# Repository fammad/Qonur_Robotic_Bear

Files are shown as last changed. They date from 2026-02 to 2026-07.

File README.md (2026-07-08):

# Qonur: Conversational AI in an Animatronic Bear




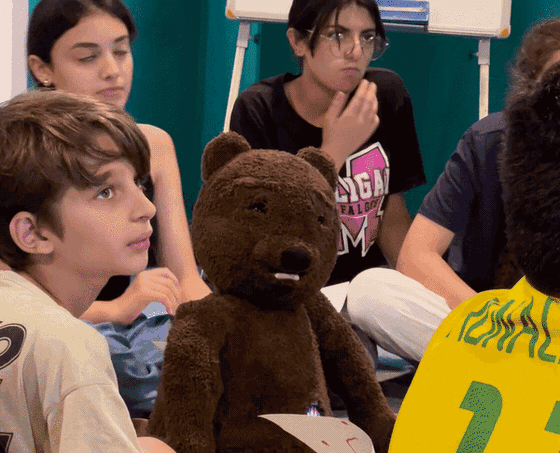
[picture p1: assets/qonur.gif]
Qonur live demo


Qonur is an AI-driven animatronic teddy bear that listens and speaks back in any language, including Azerbaijani. Behind the fur, a cloud language model, a speech pipeline, custom ESP32 firmware, and a 3D-printed actuated body run as one machine, while its mouth, eyes, and arms move in sync with the speech. It is built as a social robot for children, a familiar figure they can safely talk to about hard topics like bullying, or simply have as a friend. It performs in front of children and holds open conversations with them.

The architecture is a hybrid we call a robotic marionette. Gemini handles the conversation (speech in, generated reply, TTS out at 24 kHz) while an operator triggers arm and head gestures from a phone through Blynk. One ESP32 drives ten servos over a PCA9685 plus an 8-LED ring. A Python controller on a Raspberry Pi or laptop records the mic, calls Gemini, plays the reply, and streams mouth positions to the firmware as JSON over USB serial. The body is 3D printable from the pack in `hardware/`, about 40 cm and 2 kg in PLA.

**Watch it perform:** [live performance video](https://www.youtube.com/watch?v=doGUTJyK8F4). Same build, real audience.

## Why a marionette and not full autonomy

A cloud round trip takes several seconds and children do not wait. Scripted scenes need timing a language model will not give you. So the conversation is AI and the choreography stays human, one operator with a phone. We traded away the fully autonomous robot. In exchange, a show never stalls because the API did.

## What we tested

- The full loop on the assembled bear during live performances. Ask a question, the bear replies with moving mouth, blinking eyes, and listening LEDs.
- Two field deployments, one in a children's shelter and one in a rural village in the Lankaran region. Conversations were short-term, and the bear sometimes stayed with the children beyond the performance itself.
- The print pack on an Elegoo Neptune 4 Pro, 0.4 mm nozzle, PLA. 0.2 mm layers, 3 walls, 10 to 20 percent infill, supports only where needed.
- Not yet re-tested after this repo's code fixes: offline boot without WiFi, corrected mouth-sync duration, multi-turn conversation memory, and the inline audio path [PENDING TEST].

## Repository structure

```
main.py                    Python controller (recording, Gemini, TTS, serial)
firmware/qonur_firmware/   ESP32 sketch: servos, LEDs, serial protocol, Blynk
hardware/                  Print pack, Fusion 360 source, wiring, SETUP.md build guide
docs/                      Info pack and physical design PDFs
assets/                    Renders and demo media
```

## Build your own

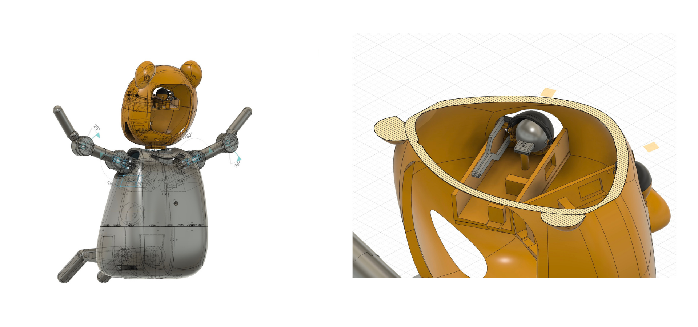
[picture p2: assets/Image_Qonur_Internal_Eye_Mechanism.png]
Internal eye mechanism


Body first. [`hardware/SETUP.md`](hardware/SETUP.md) covers printing (tested slicer settings included), what each body opening is for, assembly, and wiring. Print the pre-arranged 3MF or edit the Fusion 360 source and export your own.

Firmware. Open `firmware/qonur_firmware/qonur_firmware.ino` in Arduino IDE, install Adafruit PWM Servo Driver, Adafruit NeoPixel, ArduinoJson, and Blynk, fill in the WiFi and Blynk placeholders (optional), flash.

Controller, on Linux or Raspberry Pi:

```bash
sudo apt-get install -y portaudio19-dev libsndfile1 libasound2-dev
pip install -r requirements.txt
export GEMINI_API_KEY=your_key
python main.py
```

The bear's personality is one text block. Write your own `actor_prompt` in `main.py` and you have your own character, in whatever language and temperament you want. Set `ESP32_PORT` if your board is not on `/dev/ttyUSB0`.

The shipped defaults block content at the strictest Gemini safety thresholds, and in performances the scenario prompt further constrains what the bear says. Conversation memory is session-only and never written to disk.

## Limitations and failure analysis

- Mouth sync is open loop. Animation length comes from the PCM byte count and the pattern is a fixed 10-step sequence, so lips drift from phonemes on long replies.
- Every turn needs internet and Gemini quota. Latency stays at several seconds even with inline audio, long for a young audience.
- Push-to-talk is the Enter key in a terminal. No wake word, no voice activity detection.
- The firmware blinks autonomously every 3 seconds, holding a blocking 100 ms delay and overriding any eye command the controller sent mid-motion.
- Servos run open loop from an assumed 90 degree neutral. Skip mechanical calibration at assembly and every pose is off.
- Conversation memory re-sends recorded audio turns each request and is capped at 10 turn pairs, and the TTS cache rarely hits because replies at temperature 0.8 almost never repeat exactly.

## Future work

Long-term deployment comes first. Both field visits so far were short; the next step is leaving Qonur with a group of children for an extended period and assessing how their willingness to talk and their behaviour change over time. That requires personalization, a bear that remembers each child, which collides directly with children's data privacy. Designing that memory so no child gets profiled in the cloud is the problem we care about most.

On the technical list: a camera and a computer vision model so the bear reacts to who is in front of it, not only to voices, plus lower response latency and more expressive movement, both items that the live shows exposed.

## Status

Qonur was built and performed in 2025, in collaboration with Ritual Theater and Creativity Lab, funded by the Swiss Agency for Development and Cooperation (SDC). This repository merges the original code and mechanical design repositories, with their full history.

## Team

Fuad Mammadov and Jameel Hamzayev built and debugged the hardware and software together. Fuad led the robotics side (mechanics, 3D modeling, portable design), Jamil the AI side. Gülarə Aliyeva did 3D design and assembly, Nadejda Potaenko and Almaz Hasanzada the costume and appearance, Aynur Zarrintaj the script and dramaturgy.

## Credits & contact

Apache-2.0, see LICENSE. Credit appreciated.
Fuad Mammadov, [fammad.com](https://fammad.com) | Jameel Hamzayev, [github.com/jameelhamzayev](https://github.com/jameelhamzayev)

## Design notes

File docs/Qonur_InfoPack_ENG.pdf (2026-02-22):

Stage Performance and Role

Qonur is an inclusive actor robot bear powered by artificial intelligence. Designed for children and adolescents, Qonur takes part in story-based performances that address topics such as bullying, empathy, and awareness using the language of theater and interactive storytelling.
The teddy bear is a universal symbol of emotional comfort and safety for children. In many cultures, teddy bears are often considered a child's first friend – a symbolic figure to share fears with and feel secure around. Believing in the emotional power of this symbol, Qonur has been visually designed in the form of a teddy bear to build instant connection and trust with young audiences.
Qonur operates on a hybrid system, functioning both through AI-based automation and manual control via a mobile application, following the principles of a robotic marionette. It is portable and easy to transport. This system allows Qonur to respond dynamically to performance contexts and enables natural communication in Azerbaijani, English, and over 120 additional languages.

Based on its pre-programmed characteristics, Qonur performs as an actor in inclusive theatrical plays. It can take on the role of a narrator, a listener, or an interactive character that asks and answers questions.
While Qonur follows a prepared script, it is also able to respond adaptively and naturally to unexpected situations on stage. Although the performances initially focus on themes like inclusion and diversity, Qonur is easily adaptable to other social and educational topics in the future.

Who is Qonur and Why a Teddy Bear?

# QONUR ⁻ AI⁻Powered Robot Bear

Inclusion, Education, and Awareness Values

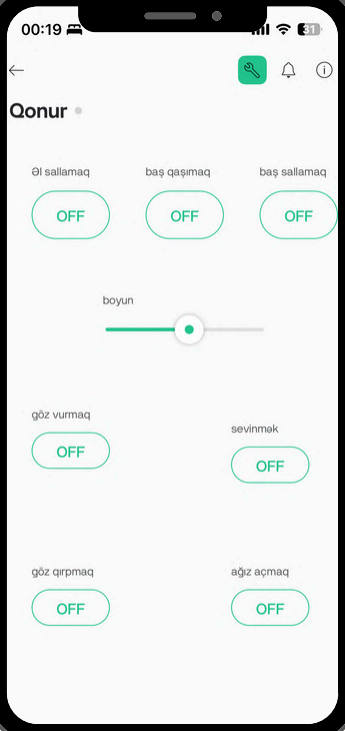
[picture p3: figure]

Technical Description (Hardware & Design) and AI Software System

Qonur is designed with an inclusive approach to openly communicate with children and adolescents who have physical and intellectual differences. Its communication style is simple, clear, and slow-paced, allowing children with diverse abilities to easily understand and respond. Through visual gestures, simplified language, eye contact, and body language, Qonur becomes accessible and understandable to all children. This helps it gain acceptance quickly, build trust, and effectively deliver inclusive educational and social messages.
Qonur serves as a practical and motivational tool in both educational and social awareness contexts. It can be used in various formats within schools, festivals, seminars, and educational laboratories—such as anti-bullying programs, empathy and social skills workshops, and as an interactive participant in robotics and technology classes.

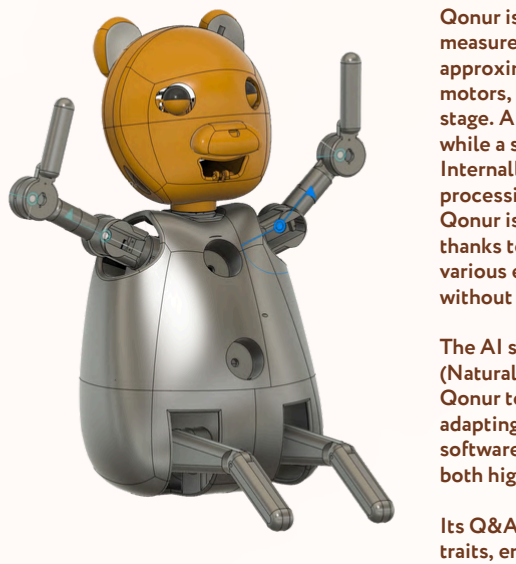
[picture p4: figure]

Qonur is built using PLA-based 3D-printed components. It measures 40 cm in height, 30 cm in width, and weighs approximately 2 kg. Its neck, arms, and eyelids move via servo motors, allowing it to perform expressive and realistic gestures on stage. A microphone is embedded in the ear section for listening, while a speaker in the chest area enables verbal responses. Internally, Qonur operates using a Raspberry Pi unit and an AI processing module.
Qonur is fully portable and can function without external power thanks to its built-in rechargeable power bank, enabling use in various environments such as schools, festivals, or open spaces without the need for cables or stationary power sources.
The AI system is built upon the Gemini API and voice-based NLP (Natural Language Processing) technologies. These tools allow Qonur to understand and respond to user questions while adapting its answers to suit the context of the performance. The software is primarily developed using Python and C++, offering both high functionality and real-time responsiveness.
Its Q&A system is based on predefined scenarios and personality traits, enabling emotionally appropriate, context-specific, and topic-relevant responses. In addition, Qonur supports openended questions, meaning it can go beyond fixed answers to engage in meaningful dialogue based on the thoughts and emotions of children and the audience.

TEAM

User and Maintenance Guide
A dedicated user manual and official website have been developed to ensure the safe and proper use of Qonur, as well as to provide access to technical support. The manual offers detailed instructions on activating the robot, powering it, connecting it to software, preparing it for performances, storage, and maintenance procedures. Additionally, the website includes supplementary materials, guides, and a FAQ section for users and professionals. Through this platform, users can both explore Qonur’s features and interact with its AIpowered chatbot.
Since Qonur’s structure is based on open-source files, educational institutions and schools can 3D print their own versions using existing 3D printers.

Fuad Mammadov – Project lead. He coordinated the work related to Qonur’s mechanical movements/structure, portable design, and 3D modeling.
Jamil Hamzayev – Robotics and software specialist. He worked on the setup of the hardware and artificial intelligence systems, as well as the integration of NLP technologies.
Gulara Aliyeva – Specialist in 3D design and assembly. She led the preparation and assembly of Qonur’s physical components and finetunings.
Nadejda Potaenko and Almaz Hasanzada – Costume and visual appearance designers. They were responsible for designing and sewing Qonur’s aesthetic look.
Aynur Zarrintaj – Scriptwriter and dramaturge. She contributed to the development of the project’s content, visual approach, and the empathetic communication abilities of the AI model.

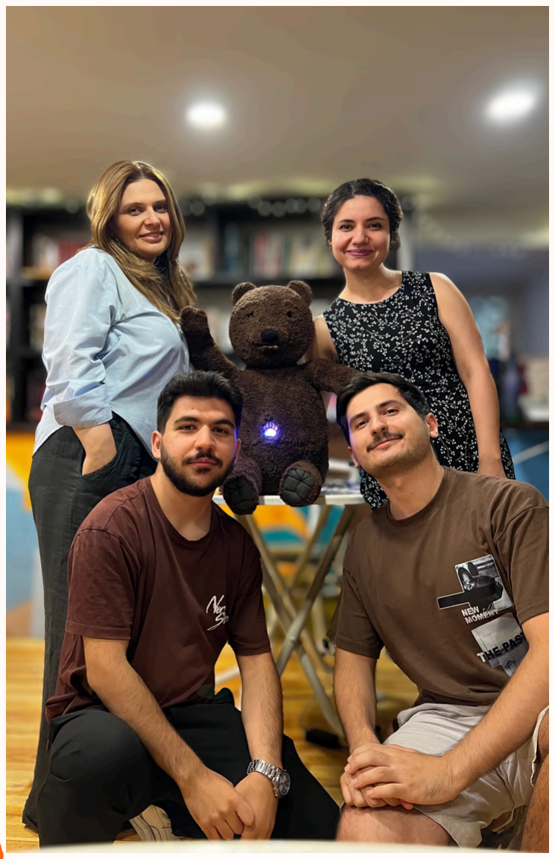
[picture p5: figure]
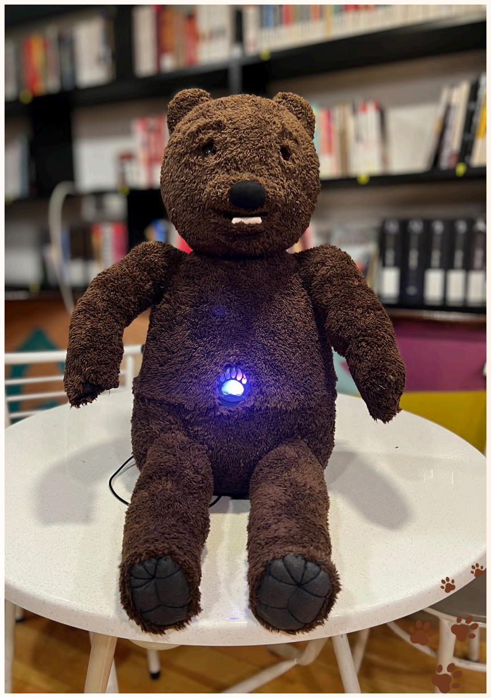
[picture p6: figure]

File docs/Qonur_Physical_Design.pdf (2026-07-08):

Robqor,ankiərəkətevə molasəsiəhərəkəteəcək.Buörədə hərəkəteəsiəzərəalınaıdı.

Ayarəcəəliəqana,molca vəiçnodilərizögöüsüeyə.

QO

Gözalıaçılıbağnıraənarını giətəküçüarçıkənarınayışdıra biəriz.Qşvəs.omtəsəniümüdü.

Burkonam
üsüüörəkob
ol.

Səsüləniciüsüarçəörüsə dəol.Cdibyamaq.

AyınınDirarəşir.Hərəkəteəcəka üsüüdinəbiərizdiəhuyət yamaq.

Boğzınotiləşənenəpaçmaıni, Motromatın

Robbonasınabəzənalalıolğıq.Oaörəsaəcəbon arıcırıriəaçılıbağnis.

BurıboşğnibəzənaralıçıxağıqOaörədəbucırıriə açılıbağnis.

Robbədəniisəyəaırıbi,zuəzənaçıbiçəkipetəri dəyişəbiək.ügöəvəalövəbunılırəzaləbiəşir.

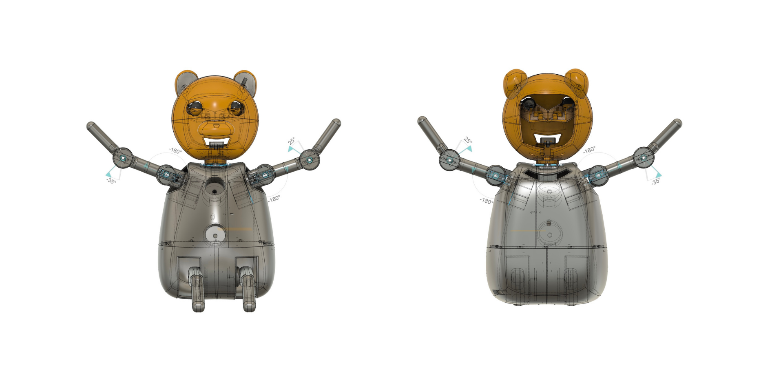
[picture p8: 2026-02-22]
assets/Image_Qonur_front-back.png

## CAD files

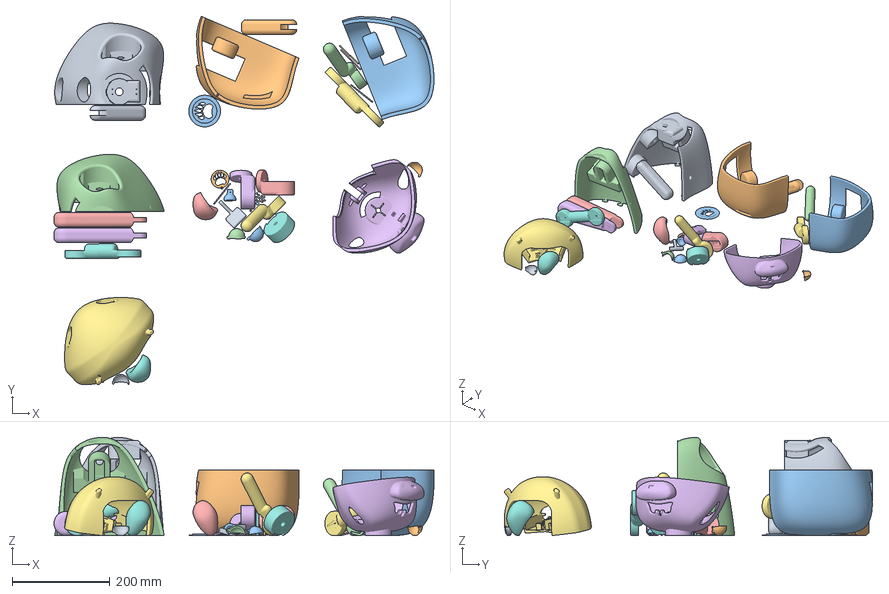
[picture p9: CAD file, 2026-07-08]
hardware/Printable_Robotic_Components.3mf
778.6 x 755.0 x 201.4 mm
Upper Body Left
Lower Body Right
Lower Body Left
Upper Body Right
Chest Emblem
ARM 0 x 2
Qonur Gift
Eye refference
Lower Arm x 2
Upper Arm x 2
Big one
Ears (1)
Lower Head
Upper Head
Right Ear
Lower Eye Lid x 2
Upper Eye Lid x 2

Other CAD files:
hardware/Editable_Components_Fusion360.f3z

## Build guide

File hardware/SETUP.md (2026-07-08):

# Building the Qonur body

Everything mechanical lives in this folder. Designed in Autodesk Fusion 360; the finished bear is about 40 cm tall and 2 kg in PLA.

## Files

- `Printable_Robotic_Components.3mf`, plates pre-arranged, open in your slicer and print.
- `Editable_Components_Fusion360.f3z`, full parametric source. Import into Fusion 360, modify parts, export your own STLs or 3MF.
- `pca9685-connection.png`, wiring diagram for the servo driver.

The design PDFs in `../docs/` cover the physical design in detail.

## Tested printing setup

Printed on an Elegoo Neptune 4 Pro with a 0.4 mm nozzle in PLA. Baseline settings that worked:

| Setting | Value |
|---|---|
| Layer height | 0.2 mm (0.16 mm for smoother finish) |
| Walls | 3 |
| Infill | 10 to 20 percent |
| Supports | only where needed |
| Brim | optional, helps on curved parts |

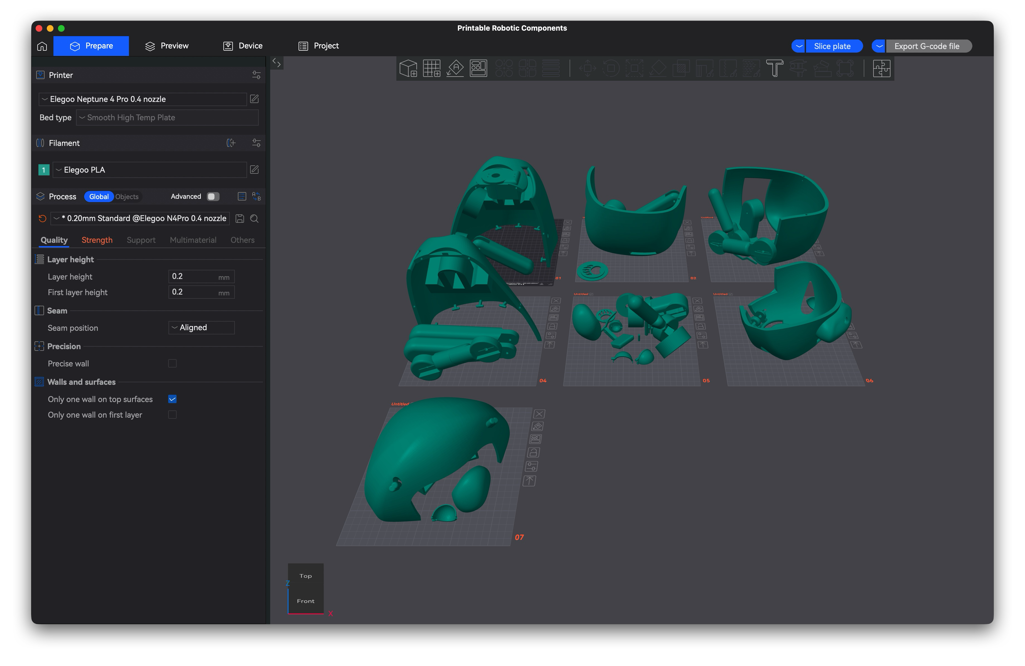
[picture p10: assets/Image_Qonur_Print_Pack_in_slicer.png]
Print pack in slicer


## What the openings are for

The body has dedicated placeholders, so plan the electronics before gluing anything.

- Ear, microphone.
- Chest, LED indicator.
- Chest circular mount, speaker.
- Back, cable and charging access.

## Assembly

Parts join with glue or with the printed connectors, whichever you prefer. The eye and mouth mechanisms are servo-driven; set every servo to 90 degrees before mounting horns, since the firmware assumes 90 as neutral. Skip this and every pose comes out wrong.

Internal eye mechanism

## Wiring

Follow `pca9685-connection.png`. ESP32 SDA/SCL to the PCA9685, WS2812 LED data on GPIO4. Servos and LEDs draw from a separate 5 to 6 V supply, common ground with the ESP32. The channel map for all ten servos is in the firmware header.

## If parts do not fit

Open a GitHub issue with your printer and material, slicer name and key settings, which file you printed, and photos of the problem.

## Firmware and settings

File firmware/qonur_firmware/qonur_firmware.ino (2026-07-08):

// Qonur robotic bear firmware (ESP32)
//
// Drives 10 servos through a PCA9685 PWM driver (I2C, address 0x40) and an
// 8-LED WS2812 ring. Accepts JSON commands over USB serial (115200) from
// main.py. Blynk app control (V1-V5) is optional: the firmware boots and runs
// the serial loop without WiFi, and attaches to Blynk when WiFi is available.
//
// PCA9685 channel map:
//   0 left_arm_shoulder   4 right_arm_wrist     7 eye_right
//   1 left_arm_elbow      5 right_arm_elbow     8 eye_left
//   2 left_arm_wrist      6 right_arm_shoulder  9 mouth
//   3 head
//
// Wiring: ESP32 SDA/SCL to PCA9685; WS2812 data on GPIO4. Servos and LEDs on
// a separate 5-6 V supply with common ground to the ESP32.
// See hardware/pca9685-connection.png.
//
// Serial JSON commands (one per line):
//   {"servo": 9, "angle": 70, "duration": 0.2}
//   {"listening": true}
//   {"state": "start_speaking"}   // also: recording_start/stop, end_speaking
//   {"reset": true}

#define BLYNK_TEMPLATE_ID   "ID"
#define BLYNK_TEMPLATE_NAME "NAME"
#define BLYNK_AUTH_TOKEN    "TOKEN"

#include <WiFi.h>
#include <BlynkSimpleEsp32.h>
#include <Wire.h>
#include <Adafruit_PWMServoDriver.h>
#include <Adafruit_NeoPixel.h>
#include <ArduinoJson.h>

char ssid[] = "SSID";
char pass[] = "PSWRD";

// LEDs
#define LED_PIN    4
#define LED_COUNT  8
Adafruit_NeoPixel pixels(LED_COUNT, LED_PIN, NEO_GRB + NEO_KHZ800);

// Servos
Adafruit_PWMServoDriver pwm = Adafruit_PWMServoDriver(0x40);
#define SERVO_COUNT      10
#define SERVO_FREQ       50
// Pulse range calibrated for the MG90S/SG90 class servos used in the build.
#define SERVO_MIN_PULSE  150
#define SERVO_MAX_PULSE  600

const char* servoNames[SERVO_COUNT] = {
  "left_arm_shoulder",   // 0
  "left_arm_elbow",      // 1
  "left_arm_wrist",      // 2
  "head",                // 3
  "right_arm_wrist",     // 4
  "right_arm_elbow",     // 5
  "right_arm_shoulder",  // 6
  "eye_right",           // 7
  "eye_left",            // 8
  "mouth"                // 9
};

// Servo motion state
int   currentPos[SERVO_COUNT];
int   targetPos[SERVO_COUNT];
int   servoSpeed[SERVO_COUNT];
bool  servoMoving[SERVO_COUNT];
unsigned long lastServoUpdate[SERVO_COUNT];

// LED state
bool        isListening      = false;
uint8_t     breathBrightness = 0;
bool        breathDir        = true;
unsigned long lastBreath     = 0;
unsigned long lastRainbow    = 0;
uint16_t    rainbowHue       = 0;

// Mouth animation
bool        mouthAnimating   = false;
unsigned long mouthLast      = 0;
int         mouthStep        = 0;
const int   mouthPatternSize = 10;
int         mouthPattern[mouthPatternSize] = {70,85,75,90,80,75,85,70,80,90};
unsigned long mouthStepDur   = 200;

// Eye blinking
unsigned long lastBlink          = 0;
const unsigned long blinkInterval = 3000; // ms
const int    blinkClosedAngle     = 0;
const int    blinkOpenAngle       = 90;

// Blynk reconnect state. Connection attempts block for up to 2 s, so retry
// sparingly and only when WiFi is up; the serial loop stays responsive.
unsigned long lastBlynkAttempt = 0;
const unsigned long blynkRetryInterval = 30000; // ms

void setServoAngle(int ch, int angle);
void moveServo(int ch, int angle, float duration);
void updateServoMovements();
void updateLEDs();
void startMouthAnimation(int durationMs);
void stopMouthAnimation();
void updateMouthAnimation();
void resetToNeutral();
void handleCommand(const String &cmd);
void handleCustomState(const String &state);

// Two-parameter overload for the Blynk handlers.
void moveServo(uint8_t ch, int angle) {
  moveServo(ch, angle, 0);
}

void setup() {
  Serial.begin(115200);
  Wire.begin();

  pwm.begin();
  pwm.setOscillatorFrequency(27000000);
  pwm.setPWMFreq(SERVO_FREQ);

  for (int i = 0; i < SERVO_COUNT; i++) {
    currentPos[i]      = 90;
    targetPos[i]       = 90;
    servoSpeed[i]      = 5;
    servoMoving[i]     = false;
    lastServoUpdate[i] = 0;
    setServoAngle(i, 90);
  }

  pixels.begin();
  pixels.show();

  // Non-blocking Blynk setup: configure only, connect from loop() when WiFi
  // is available. Blynk.begin() would block boot forever without WiFi.
  WiFi.begin(ssid, pass);
  Blynk.config(BLYNK_AUTH_TOKEN);
  Serial.println("ESP32 robot ready");
}

void loop() {
  // 1) Serial JSON commands from main.py
  if (Serial.available()) {
    String cmd = Serial.readStringUntil('\n');
    cmd.trim();
    if (cmd.length()) handleCommand(cmd);
  }

  // 2) Blynk, only when WiFi is up
  if (WiFi.status() == WL_CONNECTED) {
    if (Blynk.connected()) {
      Blynk.run();
    } else if (millis() - lastBlynkAttempt >= blynkRetryInterval) {
      lastBlynkAttempt = millis();
      Blynk.connect(2000);
    }
  }

  // 3) LEDs and mouth
  updateLEDs();
  updateMouthAnimation();

  // 4) Eye blink every 3 seconds
  unsigned long now = millis();
  if (now - lastBlink >= blinkInterval) {
    lastBlink = now;
    moveServo(7, blinkClosedAngle, 0.1);
    moveServo(8, blinkClosedAngle, 0.1);
    delay(100);
    moveServo(7, blinkOpenAngle, 0.1);
    moveServo(8, blinkOpenAngle, 0.1);
  }

  // 5) Smooth servo interpolation
  updateServoMovements();
}

void handleCommand(const String &jsonCmd) {
  StaticJsonDocument<256> doc;
  auto err = deserializeJson(doc, jsonCmd);
  if (err) {
    Serial.printf("JSON parse error: %s\n", err.c_str());
    return;
  }
  if (doc.containsKey("servo")) {
    int ch    = doc["servo"];
    int angle = doc["angle"];
    float dur = doc["duration"] | 0.5;
    if (ch >= 0 && ch < SERVO_COUNT) {
      moveServo(ch, angle, dur);
      Serial.printf("%s (ch %d) -> %d deg in %.1f s\n",
        servoNames[ch], ch, angle, dur);
    }
  }
  else if (doc.containsKey("listening")) {
    isListening = doc["listening"];
  }
  else if (doc.containsKey("state")) {
    handleCustomState(doc["state"].as<String>());
  }
  else if (doc.containsKey("reset")) {
    resetToNeutral();
  }
}

void handleCustomState(const String &state) {
  if (state == "recording_start") {
    isListening = true;
  }
  else if (state == "recording_stop") {
    isListening = false;
  }
  else if (state == "start_speaking") {
    startMouthAnimation(3000);
  }
  else if (state == "end_speaking") {
    stopMouthAnimation();
  }
}

// Blynk virtual pins: V1 wave, V2 dance, V3 head shake, V4/V5 wrist sliders
BLYNK_WRITE(V1) { if (param.asInt()) { moveServo(0,120); moveServo(1,60); delay(500); moveServo(0,90); moveServo(1,90);} }
BLYNK_WRITE(V2) { if (param.asInt()) { for (int i=0;i<3;i++){ moveServo(0,60); moveServo(1,120); moveServo(3,60); delay(300); moveServo(0,120); moveServo(1,60); moveServo(3,120); delay(300);} moveServo(0,90); moveServo(1,90); moveServo(3,90);} }
BLYNK_WRITE(V3) { if (param.asInt()) { moveServo(3,45); delay(300); moveServo(3,135); delay(300); moveServo(3,90);} }
BLYNK_WRITE(V4) { moveServo(4, param.asInt()); }
BLYNK_WRITE(V5) { moveServo(5, param.asInt()); }

void moveServo(int ch, int angle, float duration) {
  targetPos[ch] = constrain(angle, 0, 180);
  int diff = abs(targetPos[ch] - currentPos[ch]);
  // Step size per 20 ms update so the move takes roughly `duration` seconds.
  if (duration > 0 && diff > 0) servoSpeed[ch] = max(1, diff / int(duration * 50)); else servoSpeed[ch] = 10;
  servoMoving[ch] = (currentPos[ch] != targetPos[ch]);
  if (duration < 0.1) { currentPos[ch] = targetPos[ch]; setServoAngle(ch, targetPos[ch]); servoMoving[ch] = false; }
}

void updateServoMovements() {
  unsigned long now = millis();
  for (int i = 0; i < SERVO_COUNT; i++) {
    if (servoMoving[i] && now - lastServoUpdate[i] >= 20) {
      lastServoUpdate[i] = now;
      int diff = targetPos[i] - currentPos[i];
      if (abs(diff) <= servoSpeed[i]) { currentPos[i] = targetPos[i]; servoMoving[i] = false; }
      else currentPos[i] += (diff > 0 ? servoSpeed[i] : -servoSpeed[i]);
      setServoAngle(i, currentPos[i]);
    }
  }
}

void setServoAngle(int ch, int angle) {
  int pulse = map(constrain(angle, 0, 180), 0, 180, SERVO_MIN_PULSE, SERVO_MAX_PULSE);
  pwm.setPWM(ch, 0, pulse);
}

void updateLEDs() {
  unsigned long now = millis();
  if (isListening) {
    // Green breathing while recording
    if (now - lastBreath >= 30) {
      lastBreath = now;
      breathBrightness += breathDir ? 8 : -8;
      if (breathBrightness >= 200) { breathBrightness = 200; breathDir = false; }
      else if (breathBrightness <= 20) { breathBrightness = 20; breathDir = true; }
      for (int i = 0; i < LED_COUNT; i++) pixels.setPixelColor(i, pixels.Color(0, breathBrightness, 0));
      pixels.show();
    }
  } else {
    // Slow rainbow when idle
    if (now - lastRainbow >= 50) {
      lastRainbow = now;
      rainbowHue += 1024;
      for (int i = 0; i < LED_COUNT; i++) pixels.setPixelColor(i, pixels.gamma32(pixels.ColorHSV(rainbowHue + (i * 65536L / LED_COUNT))));
      pixels.show();
    }
  }
}

void startMouthAnimation(int durationMs) {
  mouthAnimating = true;
  mouthStep = 0;
  mouthLast = millis();
  mouthStepDur = max(50, durationMs / mouthPatternSize);
}

void stopMouthAnimation() {
  mouthAnimating = false;
  moveServo(9, 90, 0.3);
}

void updateMouthAnimation() {
  if (!mouthAnimating) return;
  unsigned long now = millis();
  if (now - mouthLast >= mouthStepDur) {
    mouthLast = now;
    if (mouthStep < mouthPatternSize) {
      setServoAngle(9, mouthPattern[mouthStep]);
      currentPos[9] = mouthPattern[mouthStep++];
    } else {
      stopMouthAnimation();
    }
  }
}

void resetToNeutral() {
  for (int i = 0; i < SERVO_COUNT; i++) moveServo(i, 90, 1.0);
  stopMouthAnimation();
  isListening = false;
}

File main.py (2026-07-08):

"""Qonur AI controller.

Records speech from the microphone (push-to-talk with Enter), sends it to
Gemini for a spoken reply, plays the TTS audio, and drives the bear's mouth
and eye servos over USB serial to the ESP32.

Run:
    export GEMINI_API_KEY=your_key
    python main.py

Requires an ESP32 flashed with firmware/qonur_firmware and connected via USB.
"""

import io
import json
import os
import queue
import sys
import threading
import time

import numpy as np
import pygame
import serial
import sounddevice as sd
import soundfile as sf
from scipy.io.wavfile import write
from google import genai
from google.genai import types

GOOGLE_API_KEY = os.environ.get("GEMINI_API_KEY")
if not GOOGLE_API_KEY:
    sys.exit("GEMINI_API_KEY is not set. Run: export GEMINI_API_KEY=your_key")
client = genai.Client(api_key=GOOGLE_API_KEY)

ESP32_PORT = "/dev/ttyUSB0"
ESP32_BAUDRATE = 115200
esp32_serial = None

# PCA9685 channels driven from Python. The remaining channels (arms, head)
# are handled by the firmware and the Blynk app; see firmware header for the
# full channel map.
SERVO_MAPPINGS = {
    "eye_right": 7,
    "eye_left": 8,
    "mouth": 9,
}


def connect_esp32():
    global esp32_serial
    try:
        esp32_serial = serial.Serial(ESP32_PORT, ESP32_BAUDRATE, timeout=1)
        time.sleep(2)  # ESP32 resets on serial open; give it time to boot
        print(f"Connected to ESP32 on {ESP32_PORT}")
        return True
    except Exception as e:
        print(f"Failed to connect to ESP32: {e}")
        return False


def send_servo_command(channel, angle, duration=0.5):
    if esp32_serial is None:
        print("ESP32 not connected")
        return False
    angle = max(0, min(180, angle))
    cmd = json.dumps({"servo": channel, "angle": angle, "duration": duration}) + "\n"
    esp32_serial.write(cmd.encode())
    return True


def set_led_listening_state(is_listening):
    if esp32_serial:
        esp32_serial.write((json.dumps({"listening": is_listening}) + "\n").encode())


def close_mouth():
    send_servo_command(SERVO_MAPPINGS["mouth"], 90, 0.3)


def animate_mouth_during_speech(audio_duration):
    if audio_duration <= 0:
        return
    # Fixed open/close pattern spread over the estimated speech length.
    mouth_positions = [70, 85, 75, 90, 80, 75, 85, 70, 80, 90]
    dur = max(0.1, audio_duration / len(mouth_positions))
    for i, pos in enumerate(mouth_positions):
        if i * dur >= audio_duration:
            break
        send_servo_command(SERVO_MAPPINGS["mouth"], pos, dur)
        time.sleep(dur)
    close_mouth()


def estimate_audio_duration(audio_data, sample_rate=24000, channels=1):
    # Gemini TTS returns mono 16-bit PCM at 24 kHz, so 2 bytes per sample.
    try:
        total_samples = len(audio_data) // (2 * channels)
        return max(0.5, total_samples / sample_rate)
    except Exception:
        return 2.0


# Mixer frequency must match the TTS sample rate or playback is pitch-shifted.
pygame.mixer.init(frequency=24000, size=-16, channels=2, buffer=512)
response_cache = {}


def get_cache_key(text):
    return hash(text.strip().lower())


def cache_response(text, audio_data, mime_type):
    response_cache[get_cache_key(text)] = (audio_data, mime_type)


def get_cached_response(text):
    return response_cache.get(get_cache_key(text))


def record_audio(fs=16000, channels=1):
    """Record from the microphone between two Enter presses.

    Returns the recording as WAV bytes. The listening LED stays on after
    recording stops; the main loop turns it off when the reply is ready, so
    the bear never looks frozen while the cloud is thinking.
    """
    print("Press Enter to start recording...")
    input()
    print("Recording... press Enter again to stop.")
    set_led_listening_state(True)

    frames = []

    def callback(indata, frame_count, time_info, status):
        frames.append(indata.copy())

    with sd.InputStream(samplerate=fs, channels=channels, dtype="int16", callback=callback):
        input()

    audio_data = np.concatenate(frames, axis=0)
    buf = io.BytesIO()
    write(buf, fs, audio_data)
    return buf.getvalue()


def retry_with_backoff(func, max_retries=2, base_delay=1.0, **kwargs):
    last_exc = None
    for i in range(max_retries):
        try:
            return func(**kwargs)
        except Exception as e:
            last_exc = e
            if i < max_retries - 1:
                time.sleep(base_delay * (2**i))
    raise last_exc or RuntimeError("Max retries exceeded")


def convert_and_play_audio(audio_data: bytes):
    try:
        arr = np.frombuffer(audio_data, dtype=np.int16)
        # Duplicate mono to stereo for the mixer.
        arr = np.column_stack((arr, arr))
        buf = io.BytesIO()
        sf.write(buf, arr, samplerate=24000, format="WAV")
        buf.seek(0)
        pygame.mixer.music.load(buf)
        pygame.mixer.music.play()
        while pygame.mixer.music.get_busy():
            time.sleep(0.1)
    except Exception as e:
        print(f"Playback error: {e}")


# The bear's personality lives here. Write your own prompt (character, tone,
# language, scenario rules) and you have your own bear.
actor_prompt = """PROMPT"""

# Strict blocking on all categories by default: the audience is children.
safety_settings = [
    types.SafetySetting(category=c, threshold="BLOCK_LOW_AND_ABOVE")
    for c in (
        "HARM_CATEGORY_HARASSMENT",
        "HARM_CATEGORY_HATE_SPEECH",
        "HARM_CATEGORY_SEXUALLY_EXPLICIT",
        "HARM_CATEGORY_DANGEROUS_CONTENT",
    )
]

chat_config = types.GenerateContentConfig(
    system_instruction=actor_prompt,
    safety_settings=safety_settings,
)

# Session-only conversation memory so the bear can hold a coherent multi-turn
# conversation. Nothing is written to disk. Audio turns are re-sent each
# request, so history is capped to bound cost and latency.
chat_history = []
MAX_HISTORY_ITEMS = 20  # 10 user/model turn pairs

tts_config = types.GenerateContentConfig(
    temperature=0.8,
    response_modalities=["audio"],
    speech_config=types.SpeechConfig(
        voice_config=types.VoiceConfig(
            prebuilt_voice_config=types.PrebuiltVoiceConfig(voice_name="Aoede")
        )
    ),
)
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

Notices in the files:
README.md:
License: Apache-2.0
